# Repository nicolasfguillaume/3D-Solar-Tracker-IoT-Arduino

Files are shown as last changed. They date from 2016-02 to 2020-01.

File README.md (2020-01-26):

# 3D-printed Single-axis solar tracker with Energy Storage and Bluetooth Monitoring

Solar energy is converted by the solar array and charges the Battery pack. The Battery pack is supplying a controller which optimize the orientation of the solar array towards the sunlight, based on the light sensor attached to the solar array. In addition to powering the control system, the battery pack has enough capacity to concurrently charge a smartphone or a tablet. It takes approximately about 10 hours (under STC) -or about 1.5 day- to charge the battery pack completely.

EDIT: you may find here a DRAFT version of my post on Instructables :  
https://github.com/nicolasfguillaume/3D-Solar-Tracker-IoT-Arduino/blob/master/3D-printed%20Single-axis%20Solar%20Tracker%20With%20Energy%20Storage%20and%20Bluetooth%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

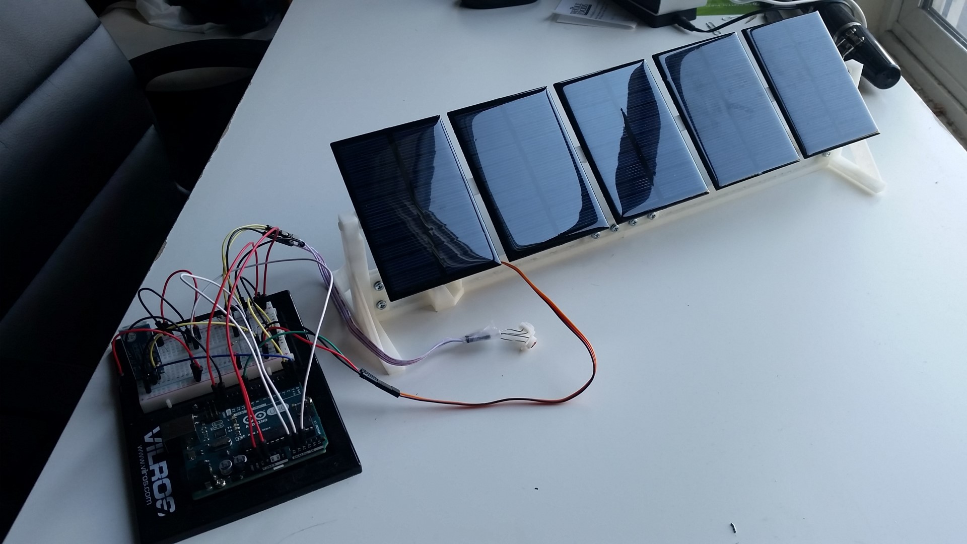
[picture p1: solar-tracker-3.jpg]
solar tracker


## Overall technical Specs

- Solar Array: 5Wp (= 5 x 1W solar panels in parallel)
- Energy Storage: 1 x 3000 mAh Lithiun Ion battery
- Controller: Arduino Uno Rev3, featuring a sun-tracking algorithm
  * Input: light sensor (2 LDR mounted at 45 degrees)
  * Output: servo motor (9g, 1.5 kg.cm)
- Monitoring: Bluetooth communication protocol (serial UART), sending data every 10 seconds
- Mounting system: 3D printed structure, featuring a fixed structure (the "base") and a moving structure (the "axis")

## Principle

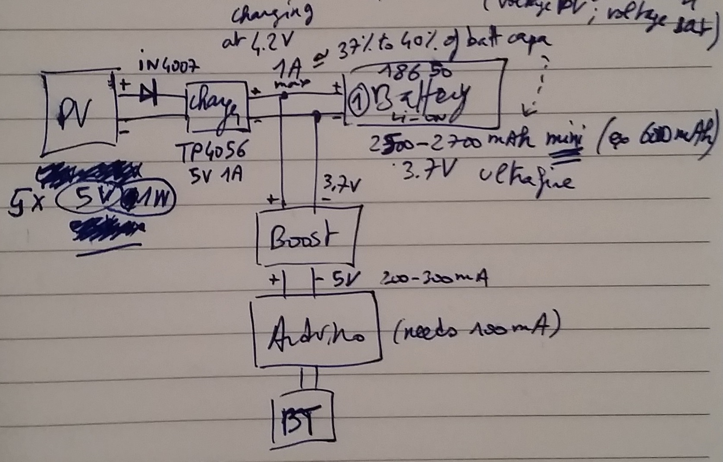
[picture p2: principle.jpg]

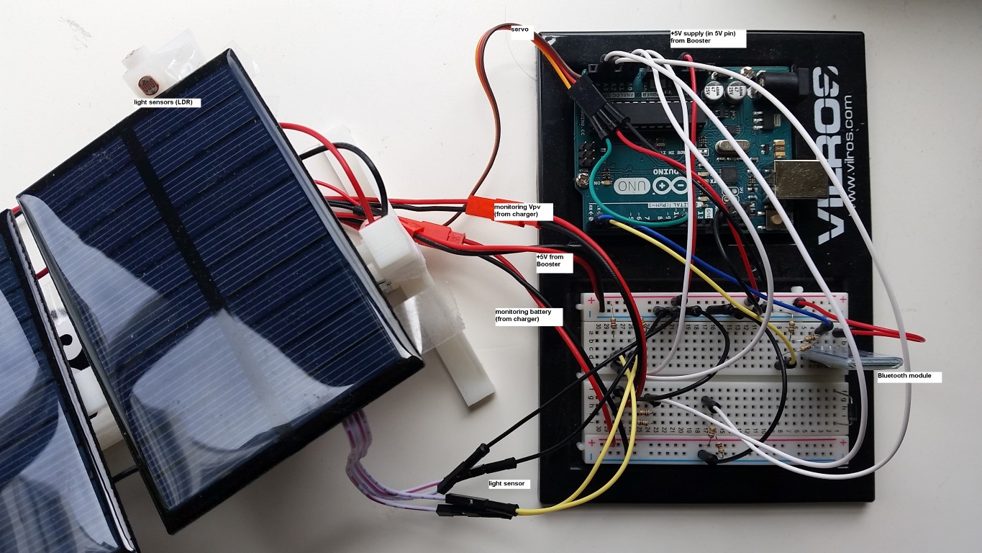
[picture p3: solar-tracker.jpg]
solar tracker


## Pictures

### Solar panels

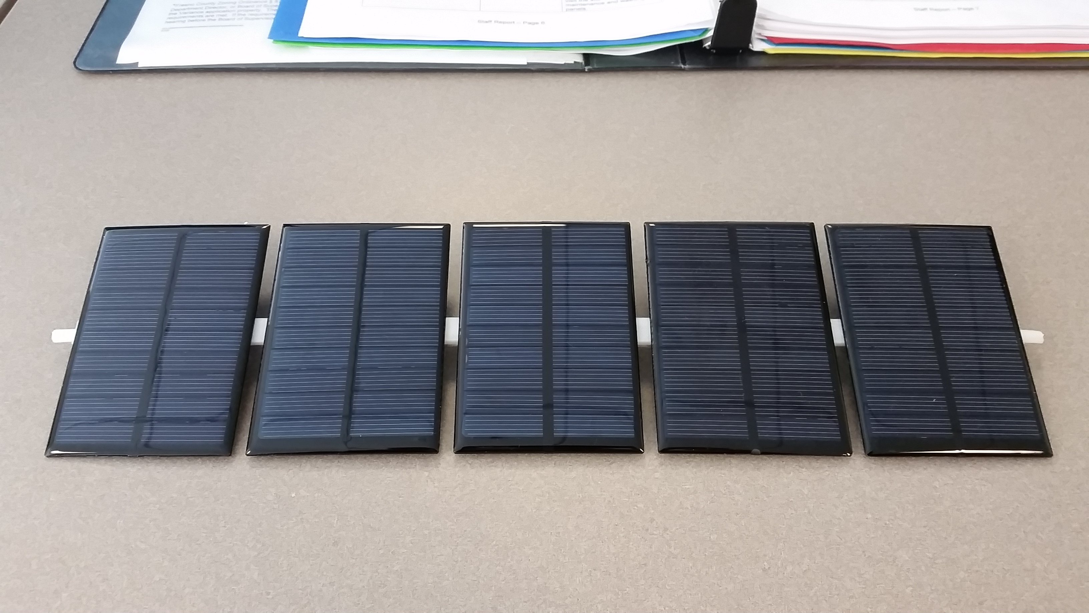
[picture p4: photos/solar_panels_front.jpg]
solar tracker

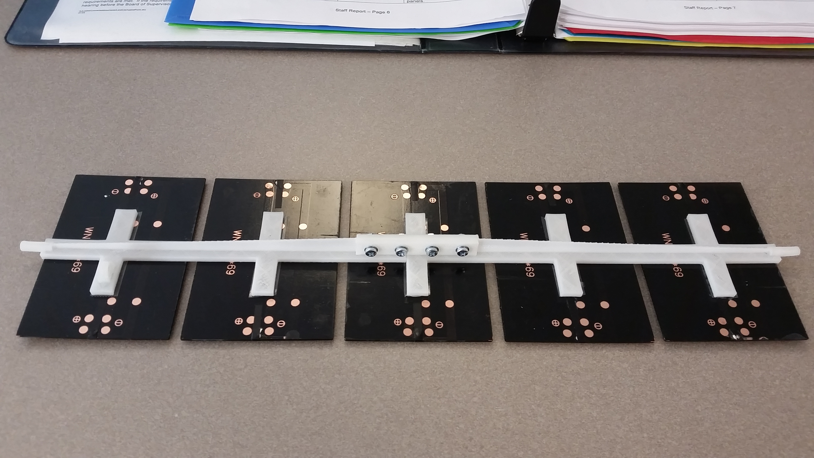
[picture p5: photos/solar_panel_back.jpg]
solar tracker


### Support and DC step motor

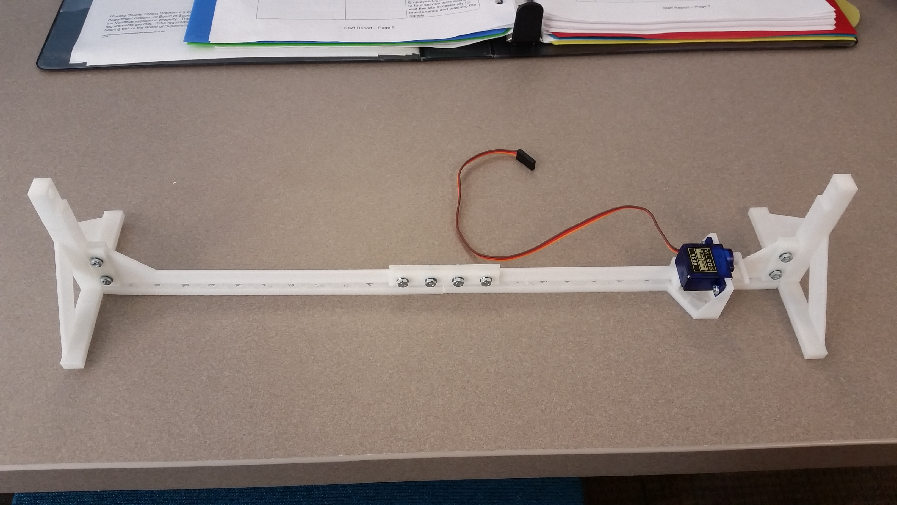
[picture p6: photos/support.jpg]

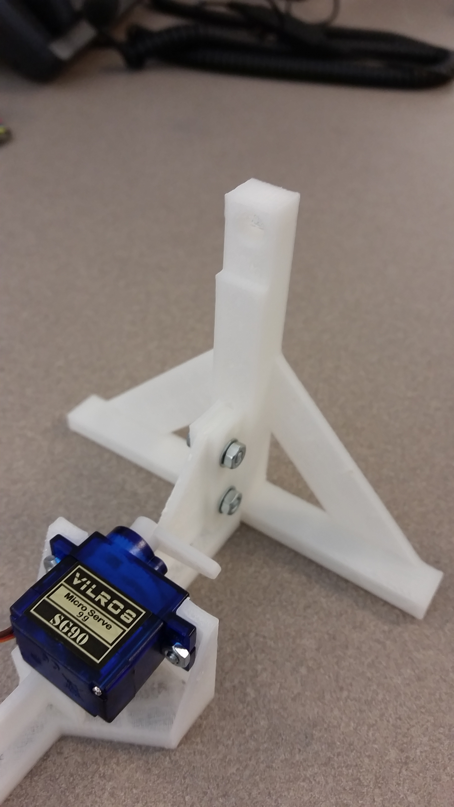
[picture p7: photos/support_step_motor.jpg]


## USB Charger

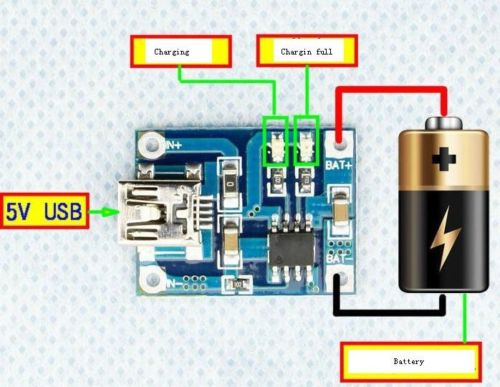
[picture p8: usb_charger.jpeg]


## Arduino files

https://github.com/nicolasfguillaume/3D-Solar-Tracker-IoT-Arduino/blob/master/solar-tracker.c

## 3D print files

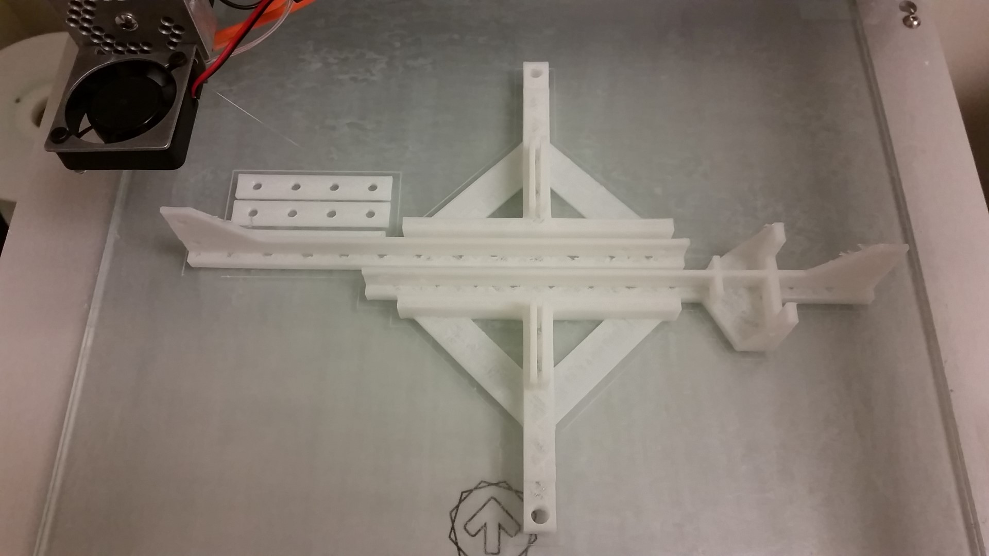
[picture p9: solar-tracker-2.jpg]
solar tracker


https://github.com/nicolasfguillaume/3D-Solar-Tracker-IoT-Arduino/blob/master/3d_print_files/Complete_Single_axis_Tracker_final.skp

Note : Sketchup files need to converted to STL files in order to sent to a 3D printer. You can use the following extension to do so : https://extensions.sketchup.com/en/content/sketchup-stl

## Solar-tracking algorithm (C programming language)

```c
  if ((abs(average_diff) >= epsilon) || (abs(-average_diff) >= epsilon))
    {
       if (average_diff > 0)
           {
             angle += servo_step;
             if(angle < 148) { myservo.write(angle); }
             else            { angle = 148; }      // low limit  --   high number is lower -- modify the design of structure to allow lower
           }
        else  
           {
             angle -= servo_step;
             if(angle > 53) { myservo.write(angle); }
             else          { angle = 53; }         // high limit -- small number is higher 
           }
       prog_speed = 200;    // faster response to a light change
    }
    else
    {
       prog_speed = prog_break;    // slower response if no major light change
    }
```

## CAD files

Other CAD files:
3d_print_files/Complete_Single_axis_Tracker_final.skp

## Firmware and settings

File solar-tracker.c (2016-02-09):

#include <Servo.h> 
#include <LowPower.h>

Servo myservo;

// Define constants
const int LDR1Pin = 0;      // define a pin for Photo resistor
const int LDR2Pin = 1;      // define a pin for Photo resistor
const int TempPin = 2;      // define a pin for Temperature sensor
const int servoPin = 9;     // define a pin for servo
const int batteryPin = 3;   // +V from battery is connected to analog pin 3
const int pvPin = 4;        // +V from pv is connected to analog pin 4

// Battery and PV monitoring
const int R1 = 10000; // value for a maximum voltage of 10 volts
const int R2 = 10000;

const int epsilon = 10;      // define tolerance (*****) -- 3 works well at noon when sunny (and on USB)
int difference = 0;        // difference between value_right and value_left // to be declared in the header only
int angle = 0;             // define angle for servo
int servo_step = 2;        // define step for servo (*****) 
long prog_speed = 200;       // define delay (ms) between two loop of the arduino program (*****)        was 200
long prog_break = 200;     // define idle time (ms) for power management -- was 8000
int angle_ref = 110;        // angle of horizontal array ; Vilros tag facing the sky

// Define BT variables
long previousMillis = 0;         // will store last time data was sent
long interval = 8000;           // interval at which to send data (ms)

// Define running average variables
const int numReadings = 6;     // number of sample for the running average (*****)     
int readings[numReadings][5];      // the readings from the 6 analog inputs
int index = 0;                  // the index of the current reading
int total[5] = { 0 };           // the running total
int average_diff = 0;           // the average of the difference

long readVcc() {
  long result;
  // Read 1.1V reference against AVcc
  ADMUX = _BV(REFS0) | _BV(MUX3) | _BV(MUX2) | _BV(MUX1);
  delay(2); // Wait for Vref to settle
  ADCSRA |= _BV(ADSC); // Convert
  while (bit_is_set(ADCSRA,ADSC));
  result = ADCL;
  result |= ADCH<<8;
  result = (1100L * 1024L) / result; // Back-calculate AVcc in mV
  return result;
}

void setup() 
{                 
  angle = angle_ref;
  myservo.attach(servoPin);
  myservo.write(angle);         // set servo to mid-point -- (panels are horizontal)
    
  pinMode(LDR1Pin, INPUT);
  pinMode(LDR2Pin, INPUT);
  pinMode(TempPin, INPUT);
  pinMode(batteryPin, INPUT);
  pinMode(pvPin, INPUT);
  Serial.begin(9600);           //Begin serial communcation
 
   // initialize all the readings for the 5 running averages: 
  for (int thisReading = 0; thisReading < numReadings; thisReading++)
      {
       for (int j = 0; j <= 5 ; j++)
         readings[thisReading][j] = 0; 
      }
} 

void loop() 
{
  //Calculate the runnning average
  //...for the light comparator
  total[0] -= readings[index][0];         // subtract the last reading:
  readings[index][0] = analogRead(LDR2Pin) - analogRead(LDR1Pin); // read the difference from the sensor: 
  total[0] += readings[index][0];         // add the reading to the total:
  //...the same for Vcc
  total[1] -= readings[index][1];         
  readings[index][1] = readVcc();                      
  total[1] += readings[index][1];       
  //...the same for Batt                     
  total[2] -= readings[index][2];         
  readings[index][2] = analogRead(batteryPin);          
  total[2] += readings[index][2];         
    //...the same for PV
  total[3] -= readings[index][3];    
  readings[index][3] = analogRead(pvPin);             
  total[3] += readings[index][3];  
  //...the same for Temp
  total[4] -= readings[index][4];         
  readings[index][4] = analogRead(TempPin);           
  total[4] += readings[index][4];  
  //...the same for A5
  //total[5] -= readings[index][5];           //ATTENTION: using the last element of the array
  //readings[index][5] = 0;                   //will mess up the calculation of the other running averages
  //total[5] += readings[index][5];           //especially average_diff 
  //...
  index += 1;                             // advance to the next position in the array:                
  if (index >= numReadings)               // at the end of the array, wrap around to the beginning:   
    index = 0;                           
  average_diff = total[0] / numReadings;     // return the runnning average of the difference
  Serial.print(average_diff ); Serial.println(" average_diff ");
  float ref_voltage = (total[1] / numReadings) / 1000.0;       // return the runnning average of Vcc
  float average_batt = total[2] / numReadings;     // return the runnning average of batt
  float average_pv = total[3] / numReadings;     // return the runnning average of batt
  //float average_temp = total[4] / numReadings;     // return the runnning average of temp
    
  if ((abs(average_diff) >= epsilon) || (abs(-average_diff) >= epsilon))
    {
       if (average_diff > 0)
           {
             angle += servo_step;
             if(angle < 148) { myservo.write(angle); }
             else            { angle = 148; }      // low limit  --   high number is lower -- modify the design of structure to allow lower
           }
        else  
           {
             angle -= servo_step;
             if(angle > 53) { myservo.write(angle); }
             else          { angle = 53; }         // high limit -- small number is higher 
           }
       prog_speed = 200;    // faster response to a light change
    }
    else
    {
       prog_speed = prog_break;    // slower response if no major light change
    }

   //Update temperature
    //float voltage_temp = average_temp * ref_voltage / 1024.0;
    //float temperatureC = (voltage_temp - 0.5) * 100 ;  //converting from 10 mv per degree with 500 mV offset

   //Update battery capacity %
    float voltage_batt = average_batt * ref_voltage * 2.0 / 1024.0; //    /(R2/(R1 + R2)) 
    float battery_capa = (voltage_batt - 3.0) * (100 - 0) / (4.2 - 3.0);

   //Update PV voltage
    float voltage_pv = average_pv * ref_voltage * 2.0 / 1024.0; //    /(R2/(R1 + R2)) 
    float power_pv = voltage_pv * 0.150 * 5;
    
    //Correct angle for display
    float angle_corr = angle * (148 - 110) / 45 - 100 * (148 - 110) / 45;

   //Datalogging over bluetooth
   unsigned long currentMillis = millis();
   unsigned long currentTime = millis() / 1000.0;
   if(currentMillis - previousMillis > interval) 
   {
    previousMillis = currentMillis;   
    Serial.print("Time = "); Serial.print(millis()/1000.0); Serial.print(" s       |  ");
    Serial.print("Array angle = "); Serial.print(angle_corr); Serial.println(" deg");
    //Serial.print("Temperature = "); Serial.print(temperatureC); Serial.println(" deg C");
    Serial.print("Battery SOC = "); Serial.print( (int) battery_capa); Serial.print("%  |  ");
    Serial.print("V batt = "); Serial.print(voltage_batt); Serial.println(" V");
    Serial.print("V pv = "); Serial.print(voltage_pv); Serial.print(" V        |  ");
    Serial.print("P pv (estimate) = "); Serial.print(power_pv); Serial.println(" W");
    Serial.print("Vcc = "); Serial.print(ref_voltage); Serial.println(" V");
    Serial.println();
  }
  
   // Power Management
   if (prog_speed == 200)
   {
      delay(prog_speed); //short delay for faster response to light
      //LowPower.powerDown(SLEEP_60MS, ADC_OFF, BOD_OFF);  // sleep for 15, 30 or 60 msec
   }
   else if (currentTime > 10)                  // slower response if no major light change
   {
      Serial.print("Sleep for 8 sec...");
      delay(50);
      LowPower.powerDown(SLEEP_8S, ADC_OFF, BOD_OFF);  // sleep for 1, 2, 4 or 8 sec
      //delay(prog_break);
      Serial.println(" Waking up!"); Serial.println("");
      prog_speed == 200 ;  // back to a faster response
   }
